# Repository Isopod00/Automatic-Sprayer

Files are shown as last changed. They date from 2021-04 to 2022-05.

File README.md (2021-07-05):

# Automatic Sprayer
Created By Anthony Brogni

This is my Automatic Sprayer project. I originally made a prototype of this project in 2017 but was not completely satisfied with the results, so I decided to go back and improve it. I have been making changes to this project ever since, and I believe it has been greatly improved over the past four years. This project is an Arduino-controlled automatic sprayer that can keep plants and pets hydrated while you're away from home. When you first plug it in you are prompted to configure the system, and then after that, you're good to go! Some features of this project are spray scheduling and spray duration control, a visual countdown clock to the next spray, and a manual spray button. Another notable feature that I recently added is Wifi connectivity so that the project can connect to the user's home Wifi network, enabling over-the-air software updates. In addition to over-the-air software updates, Wifi connectivity also allows the project to connect to the Adafruit IO web service for control over wifi. This means that by using my phone from anywhere in the world, as long as I am connected to the internet, I can trigger the sprayer to start spraying! Using the IFTTT service, I have also connected the project to Amazon Alexa, allowing me to trigger sprays by giving a voice command to my Alexa-enabled devices. As you can see, there are multiple ways to control my automatic sprayer project, which makes it easy and convenient to use for everyone!

<p align="center">
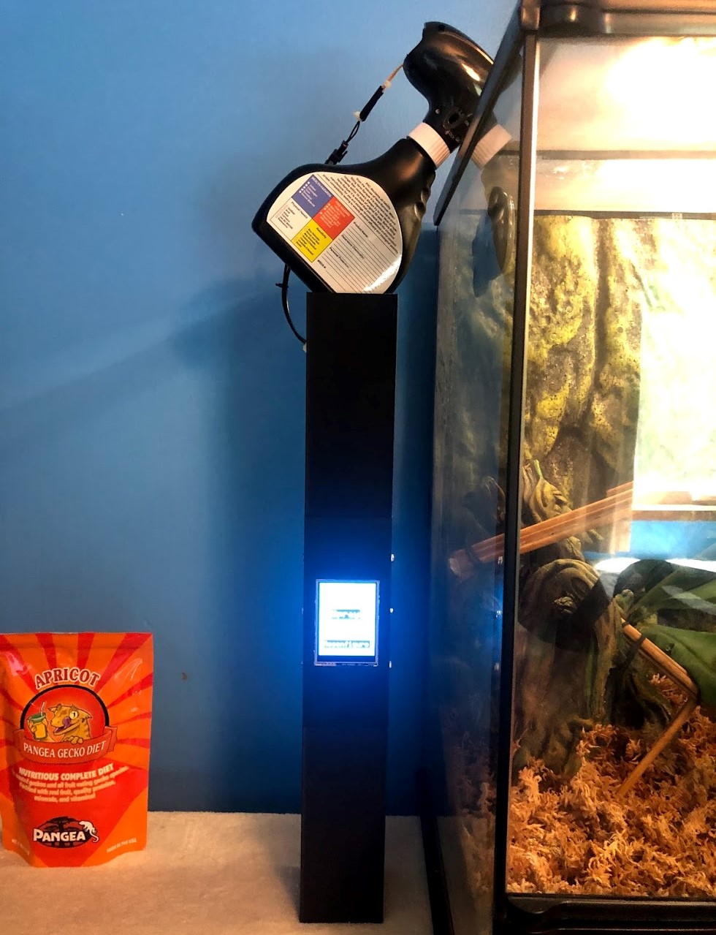
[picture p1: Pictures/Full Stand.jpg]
Sprayer Stand
   
</p>

### Code

All of the code for this project is contained in a single [.ino script](https://github.com/Isopod00/Automatic-Sprayer/blob/Wifi-Enabled/Code/AutomaticSprayer/AutomaticSprayer.ino) that is run by an Arduino Mega 2560. 

The main functions of the code are to:
  1. Connect to my home wifi network to allow for over-the-air software updates
  2. Connect to the Adafruit IO service to allow for commands to be sent over Wifi
  3. Allow the user to configure system settings such as the interval between sprays and the spray duration using the touch screen
  4. Keep track of the time remaining until the next spray and display it to the user on the touch screen
  5. Allow the user to manually initiate a spray whenever they want via a digital button on the touch screen

The code for this project utilizes the Elegoo_GFX, Elegoo_TFTLCD, Touchscreen, WiFi101, ArduinoOTA, and Adafruit_MQTT libraries, all of which can be found [here](https://github.com/Isopod00/Automatic-Sprayer/tree/Wifi-Enabled/Code/Libraries) in the project repository. The SPI library is also used, which is included in the Arduino IDE by default.

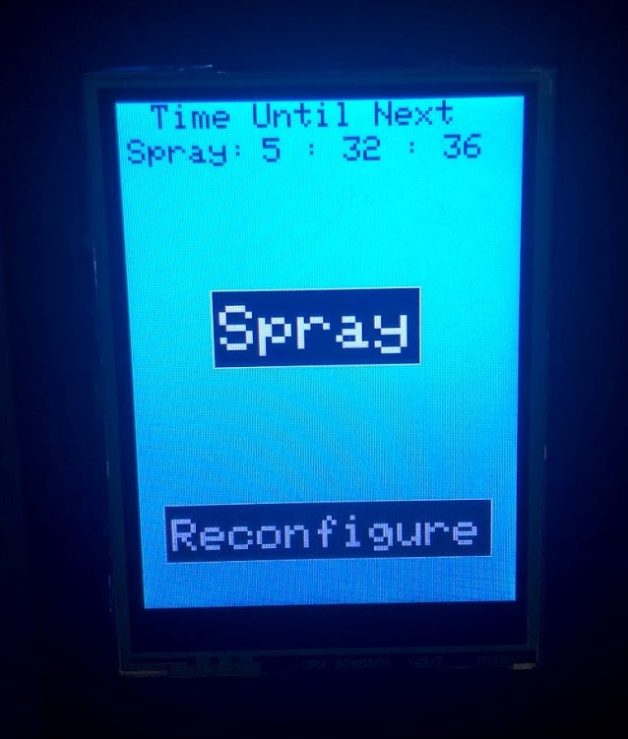
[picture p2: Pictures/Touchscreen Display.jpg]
Touchscreen Display
 

<p>&nbsp;</p>

### Electronics

The electronic components used in this project are:
  1. [Arduino MEGA 2560 REV3](https://www.amazon.com/ELEGOO-ATmega2560-ATMEGA16U2-Projects-Compliant/dp/B01H4ZLZLQ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)
  2. [ELEGOO 2.8 Inch TFT LCD Touch Screen](https://www.amazon.com/Elegoo-EL-SM-004-Inches-Technical-Arduino/dp/B01EUVJYME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)
  3. [L298N Motor Driver Board](https://www.amazon.com/HiLetgo-Controller-Stepper-H-Bridge-Mega2560/dp/B07BK1QL5T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)
  4. [3.3v/5v Power Supply Module](https://www.amazon.com/JBtek-Breadboard-Supply-Arduino-Solderless/dp/B010UJFVTU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)
  5. [Motorized Spray Bottle](https://www.amazon.com/Dynamic-1-touch-multi-purpose-motorized-bottle/dp/B01LXJ0SPG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)
  6. [ELEGOO 9V 1A Barrel Plug Power Adapter](https://www.amazon.com/ELEGOO-100V-240V-Converter-Adapter-Certificate/dp/B074BRR5YN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)
  7. [DC Barrel Plug Splitter](https://www.amazon.com/PHC-DC-3Y-Barrel-Splitter-Female/dp/B009AZZ4ES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)
  8. [Flexible Breadboard Jumper Wires](https://www.amazon.com/Elegoo-EL-CP-004-Multicolored-Breadboard-arduino/dp/B01EV47GI4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)
  9. [Adafruit ATWINC1500 WiFi Breakout Board](https://www.amazon.com/Adafruit-2999-ATWINC1500-WiFi-Breakout/dp/B01GVI1NKA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)

<p>&nbsp;</p><p>&nbsp;</p><p>&nbsp;</p>

<p align="center">
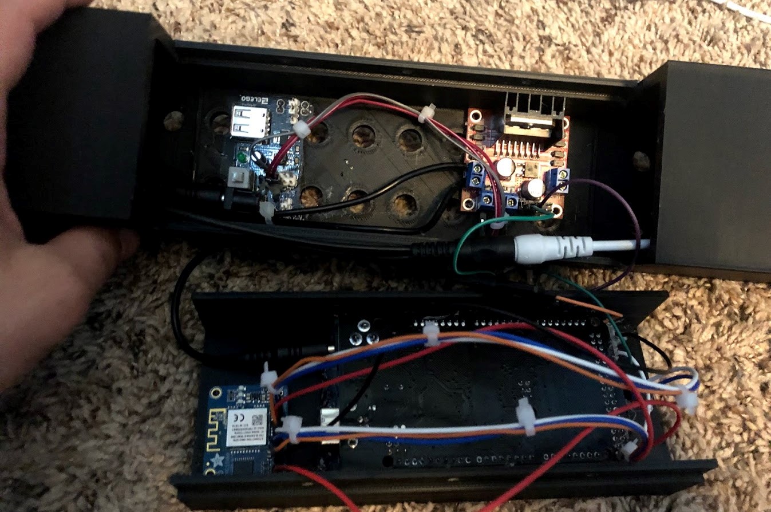
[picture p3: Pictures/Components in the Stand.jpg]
Electronic Components
   
</p>

### 3D Printed Parts

For this project I designed and 3D Printed a stand for the sprayer that also houses the electronics inside of it to keep everything compact.
 
<p align="center">
  <b>CAD Program Used:</b> Fusion 360 &nbsp;&nbsp;&nbsp;&nbsp;&nbsp;
  <b>Slicer Program Used:</b> Ultimaker Cura <br>                                             
  <b>3D Printer Used:</b> Ender 5 Pro &nbsp;&nbsp;&nbsp;&nbsp;&nbsp;
  <b>Filament Used:</b> Black PLA <br><br>
  All of the STL and sliced G-Code files can be found <a href="https://github.com/Isopod00/Automatic-Sprayer/tree/Wifi-Enabled/CAD%20Files">here</a> in the project repository.
</p>

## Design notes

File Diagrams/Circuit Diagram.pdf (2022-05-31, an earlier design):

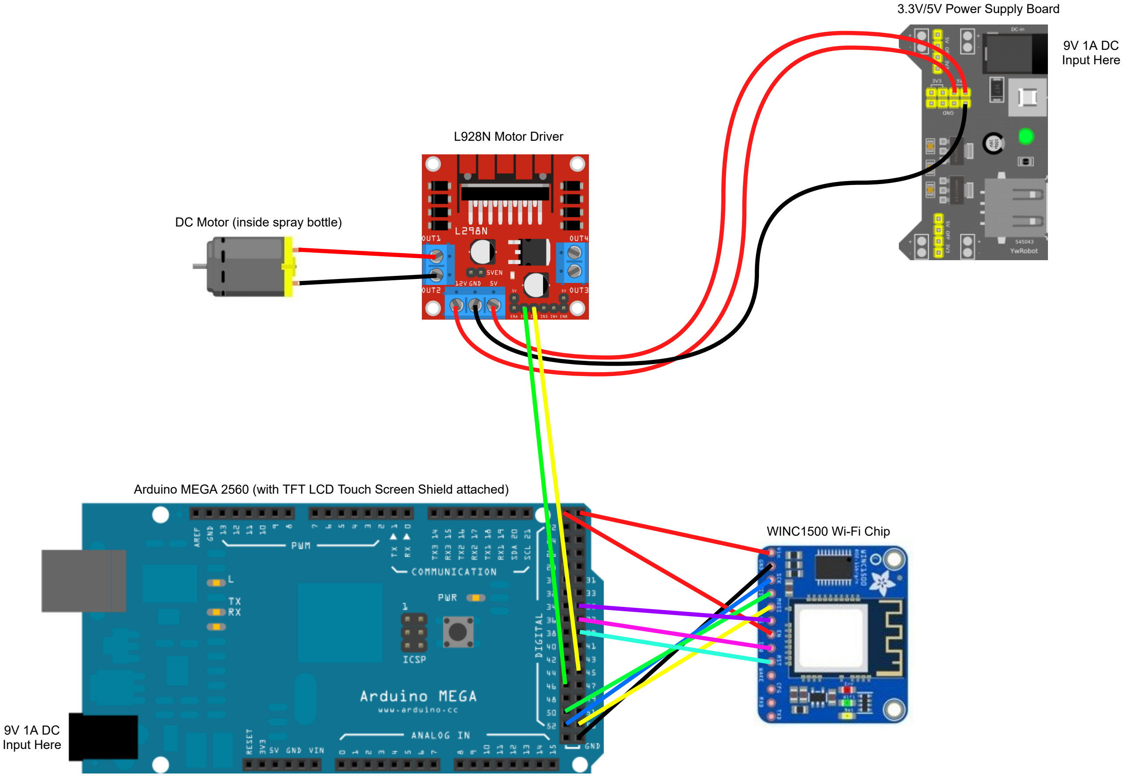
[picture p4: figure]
L928N Motor Driver; DC Motor (inside spray bottle); WINC1500 Wi-Fi Chip; 3.3V/5V Power Supply Board; 9V 1A DC Input Here

Arduino MEGA 2560 (with TFT LCD Touch Screen Shield attached)

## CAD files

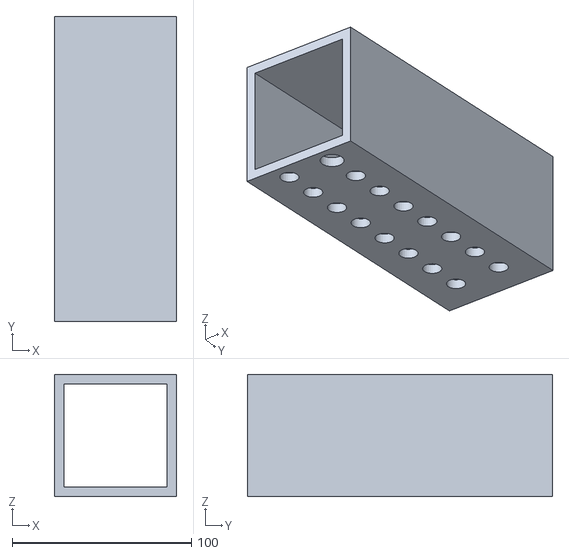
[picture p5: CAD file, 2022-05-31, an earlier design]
CAD Files/STL Files/Stand_Base.stl
68.0 x 170.0 x 68.0

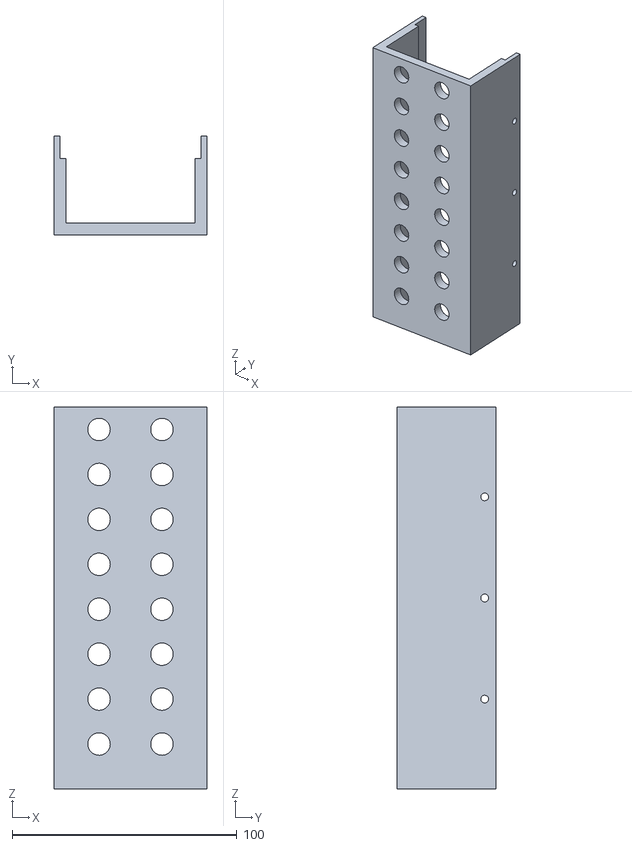
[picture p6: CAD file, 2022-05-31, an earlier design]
CAD Files/STL Files/Stand_Electronics_Back.stl
68.0 x 44.0 x 170.0

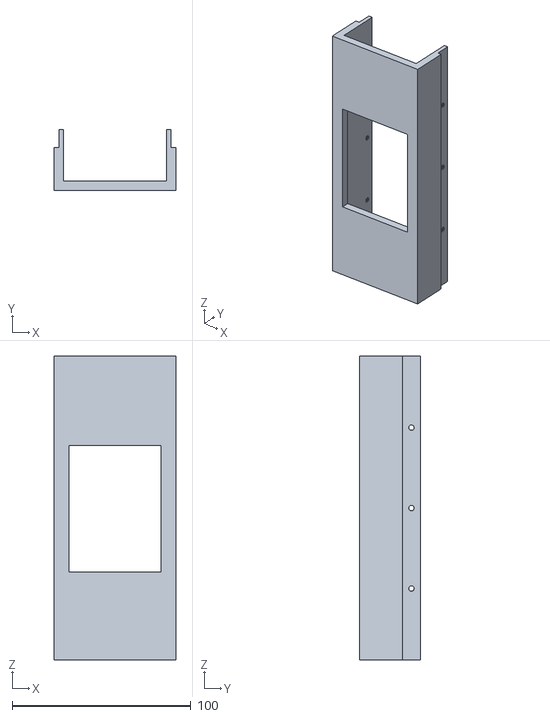
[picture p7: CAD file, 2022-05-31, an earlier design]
CAD Files/STL Files/Stand_Electronics_Front.stl
68.0 x 34.0 x 170.0

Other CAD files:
CAD Files/STL Files/Stand_Top.stl

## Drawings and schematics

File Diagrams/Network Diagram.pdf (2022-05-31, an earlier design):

# Cloud Services

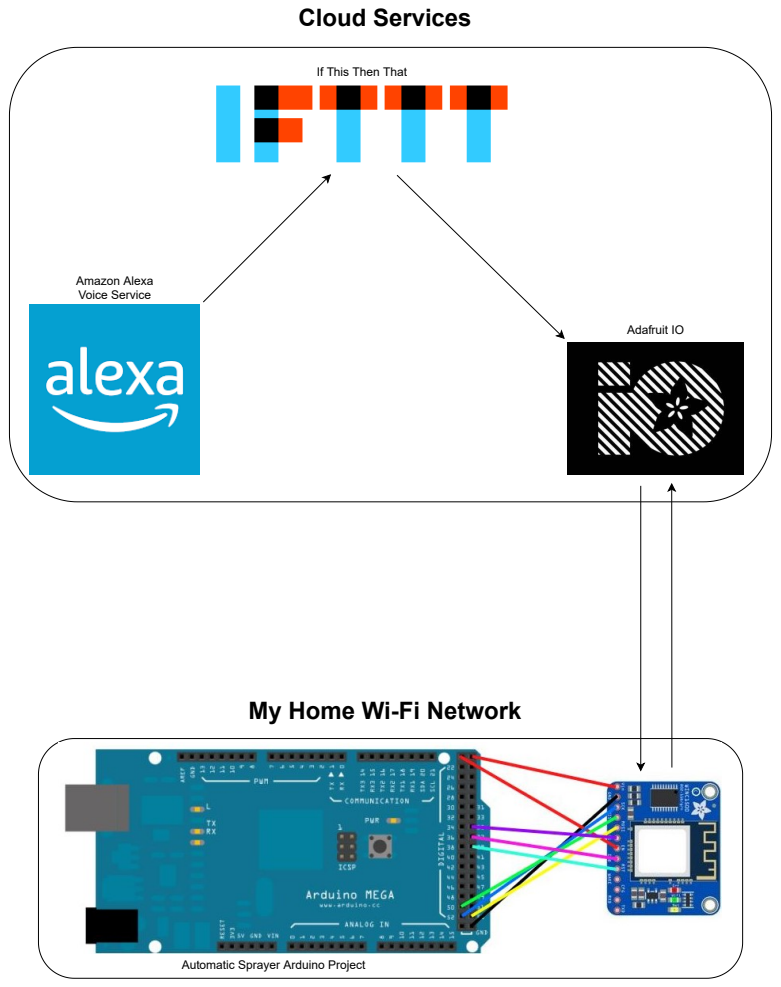
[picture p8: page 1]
Amazon Alexa Voice Service; Adafruit IO

If This Then That

My Home Wi-Fi Network

Automatic Sprayer Arduino Project

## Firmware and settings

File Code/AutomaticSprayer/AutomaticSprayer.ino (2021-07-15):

//Automatic Sprayer
//By Anthony Brogni

#include <Elegoo_GFX.h>    // Core graphics library
#include <Elegoo_TFTLCD.h> // Hardware-specific library
#include <TouchScreen.h>   // Core (non-specific) touchscreen library

// Libraries required for WiFi connectivity & OTA updates //
#include <SPI.h>
#include <WiFi101.h>
#include <ArduinoOTA.h>

// Libraries Required for integration with Adafruit.io //
#include "Adafruit_MQTT.h"
#include "Adafruit_MQTT_Client.h"

// Enter sensitive data (like WiFi name & password) in the secrets tab (arduino_secrets.h) //
#include "arduino_secrets.h" 

// Wifi Settings //
char ssid[] = SECRET_SSID; // WiFi network SSID (name)
char pass[] = SECRET_PASS; // WiFi network password
int status = WL_IDLE_STATUS;

// Adafruit.io Settings //
#define AIO_SERVER      "io.adafruit.com"
#define AIO_SERVERPORT  1883
#define AIO_USERNAME    SECRET_USERNAME
#define AIO_KEY         SECRET_KEY

//Set up the wifi client
WiFiClient client;
Adafruit_MQTT_Client mqtt(&client, AIO_SERVER, AIO_SERVERPORT, AIO_USERNAME, AIO_KEY);

#define MQTT_CONN_KEEPALIVE 43200; //The server will keep the socket open, unless it has not heard from the device in 12 hours

// Adafruit.io Feeds //
Adafruit_MQTT_Subscribe sprayStatus = Adafruit_MQTT_Subscribe(&mqtt, AIO_USERNAME "/feeds/spraying");
Adafruit_MQTT_Publish confirmSpray = Adafruit_MQTT_Publish(&mqtt, AIO_USERNAME "/feeds/sprayconfirmed");

const int totalSprayTime = 825; // Measured in seconds
int remainingSprays;

// The control pins for the LCD can be assigned to any digital or analog pins, but using the analog pins allows for doubling up the pins with the touch screen (see the TFT paint example).
#define LCD_CS A3 // Chip Select goes to Analog 3
#define LCD_CD A2 // Command/Data goes to Analog 2
#define LCD_WR A1 // LCD Write goes to Analog 1
#define LCD_RD A0 // LCD Read goes to Analog 0

#define LCD_RESET A4 // Can alternately just connect to Arduino's reset pin

#define YP A2  // must be an analog pin, use "An" notation!
#define XM A3  // must be an analog pin, use "An" notation!
#define YM 8   // can be a digital pin
#define XP 9   // can be a digital pin

// The min and max values for the x and y coordinates of the touchscreen //
#define TS_MINX 130
#define TS_MINY 130
#define TS_MAXX 940
#define TS_MAXY 940

// Assign human-readable names to some common 16-bit color values //
#define BLACK   0x0000
#define BLUE    0x001F
#define RED     0xF800
#define GREEN   0x07E0
#define CYAN    0x07FF
#define MAGENTA 0xF81F
#define YELLOW  0xFFE0
#define WHITE   0xFFFF

#define BACKGROUNDCOLOR CYAN // Customize the background color of the display!
#define TEXTCOLOR BLACK // Customize the color of text that is displayed!

Elegoo_TFTLCD tft(LCD_CS, LCD_CD, LCD_WR, LCD_RD, LCD_RESET);
TouchScreen ts = TouchScreen(XP, YP, XM, YM, 300);

int hours = 8;
int minutes = 0;
int seconds = 0;

int time = 0;
int waitTime = 0;
int wait = 15000;

int motor = 46;
int motorPin2 = 45;

bool spraying = false;

int assignedHours = 8;
int assignedWait = 15000;

bool answered1 = false;
bool answered2 = false;
bool answered3 = false;
bool answered4 = false;

void setup() {
  WiFi.setPins(35,37,39); // Configure pins for the Adafruit ATWINC1500 Breakout
  
  Serial.begin(9600); // Initialize serial 

  connectToNetwork(); // Connect to home WiFi network

  tft.reset();

  pinMode(motor, OUTPUT);
  pinMode(motorPin2, OUTPUT);

  digitalWrite(motorPin2, LOW);

  mqtt.subscribe(&sprayStatus);

  uint16_t identifier = tft.readID();
  if (identifier == 0x9325) {
  } else if (identifier == 0x9328) {
  } else if (identifier == 0x4535) {
  } else if (identifier == 0x7575) {
  } else if (identifier == 0x9341) {
  } else if (identifier == 0x8357) {
  } else if (identifier == 0x0101) {
    identifier = 0x9341;
  }
  else {
    identifier = 0x9341;
  }
  tft.begin(identifier);
  
  boot();
  configSystem();

  remainingSprays = totalSprayTime / (assignedWait / 1000); // divide by 1000 converts milliseconds to seconds
}

void loop() {
  if (status == WL_CONNECTED) { 
    ArduinoOTA.poll(); // Check for OTA updates over WiFi
    MQTT_connect(); // Connect or Reconnect to the MQTT service
  } else {
    connectToNetwork(); // Try reconnecting to home WiFi network
  }
  
  Adafruit_MQTT_Subscribe *subscription;
  subscription = mqtt.readSubscription();

  if (subscription == &sprayStatus) {
    if (0 == strcmp((char *)sprayStatus.lastread, "ON")) {
      spray();
    }
  }

  // Check for button presses and add time to the loop so counting by seconds is accurate //
  buttonPress();
  delay(5);
  if (time == 60) {
    time = 0;
    subtractTime();
  }
  else {
    time++;
  }
}

void connectToNetwork() {
  // Check if the WiFi board is connected //
  if (WiFi.status() != WL_NO_SHIELD) {
    
    // Attempt to connect to Wifi network //
  while (status != WL_CONNECTED) {
    Serial.print("Attempting to connect to SSID: ");
    Serial.println(ssid);
    status = WiFi.begin(ssid, pass); // Connect to WPA/WPA2 network. Change this line if using open or WEP network
  }
  
  Serial.print("Successfully connected to SSID: ");
  Serial.print(WiFi.SSID());
  Serial.println("!");

  // start the WiFi OTA library with internal (flash) based storage
  ArduinoOTA.begin(WiFi.localIP(), "Arduino", "password", InternalStorage);
  }
}
  
void boot() {
  tft.fillScreen(BACKGROUNDCOLOR);
  tft.setRotation(2);
  tft.setCursor(20, 2);
  tft.setTextColor(TEXTCOLOR);
  tft.setTextSize(2);
  tft.println("Automatic Sprayer");
  tft.setCursor(100, 22);
  tft.println("v3.5");
  tft.setCursor(80, 280);
  tft.println("Made by");
  tft.setCursor(40, 300);
  tft.println("Anthony Brogni");
  tft.setCursor(30, 140);
  tft.setTextSize(4);
  tft.println("Welcome!");
  delay(4000);
}

// Function used to connect and reconnect as necessary to the MQTT server //
void MQTT_connect() {
  // Stop if already connected.
  if (mqtt.connected()) {
    return;
  }

  Serial.print("Connecting to MQTT... ");

  if(mqtt.connect() == 0) {
    Serial.println("MQTT Connected!");
  } else {
    Serial.println("Connect to MQTT FAILED");
  }
}

void configSystem() {
  assignedHours = 8;
  assignedWait = 15000;

  tft.fillScreen(BACKGROUNDCOLOR);
  tft.setCursor(20, 2);
  tft.setTextSize(2);
  tft.println("The default spray");
  tft.setCursor(15, 22);
  tft.println("interval is every");
  tft.setCursor(50, 42);
  tft.println("eight hours.");
  tft.setCursor(20, 102);
  tft.println("Would you like it");
  tft.setCursor(20, 122);
  tft.println("to stay that way?");
  drawButton(20, 210, 80, 50, 4, "Yes", 0);
  drawButton(140, 210, 80, 50, 4, "No", 15);
  while (!answered1) {
    if (status == WL_CONNECTED) { 
      ArduinoOTA.poll(); //Check for WiFi OTA updates
    }
  
    TSPoint p = ts.getPoint();

    if (p.z > ts.pressureThreshhold) {
      if (p.x > 280 && p.x < 400 && p.y > 185 && p.y < 420) {
        //This is important because the tft and touchscreen libraries are sharing pins
        pinMode(XM, OUTPUT);
        pinMode(YP, OUTPUT);

        answered1 = true;

        tft.fillScreen(BACKGROUNDCOLOR);
        config2();
      }
      else if (p.x > 255 && p.x < 385 && p.y > 610 && p.y < 860) {
        //This is important because the tft and touchscreen libraries are sharing pins
        pinMode(XM, OUTPUT);
        pinMode(YP, OUTPUT);

        answered1 = true;

        tft.fillScreen(BACKGROUNDCOLOR);

        tft.setCursor(0, 0);
        tft.setTextSize(2);
        tft.println("How many hours would");
        tft.setCursor(5, 20);
        tft.println("you like to set the");
        tft.setCursor(10, 40);
        tft.println("spray interval to?");

        drawButton(15, 120, 50, 50, 4, "2", 8);
        drawButton(95, 120, 50, 50, 4, "4", 8);
        drawButton(175, 120, 50, 50, 4, "6", 8);
        drawButton(15, 200, 50, 50, 4, "8", 8);
        drawButton(95, 200, 50, 50, 4, "10", -3);
        drawButton(175, 200, 50, 50, 4, "12", -3);

        while (!answered2) {
          if (status == WL_CONNECTED) { 
            ArduinoOTA.poll(); //Check for WiFi OTA updates
          }
  
          TSPoint p = ts.getPoint();

          if (p.z > ts.pressureThreshhold) {
            //This is important because the tft and touchscreen libraries are sharing pins
            pinMode(XM, OUTPUT);
            pinMode(YP, OUTPUT);
            
            if (p.x > 520 && p.x < 640 && p.y > 180 && p.y < 295) {
              answered2 = true;
              assignedHours = 2;
            }
            else if (p.x > 520 && p.x < 640 && p.y > 445 && p.y < 580) {
              answered2 = true;
              assignedHours = 4;
            }
            else if (p.x > 520 && p.x < 640 && p.y > 700 && p.y < 850) {
              answered2 = true;
              assignedHours = 6;
            }
            else if (p.x > 285 && p.x < 430 && p.y > 180 && p.y < 295) {
              answered2 = true;
              assignedHours = 8;
            }
            else if (p.x > 285 && p.x < 430 && p.y > 445 && p.y < 580) {
              answered2 = true;
              assignedHours = 10;
            }
            else if (p.x > 285 && p.x < 430 && p.y > 700 && p.y < 850) {
              answered2 = true;
              assignedHours = 12;
            }
            if (answered2) {
              tft.fillScreen(BACKGROUNDCOLOR);
              config2();
            }
          }
        }
      }
    }
  }
}

void subtractTime() {
  if (seconds == 0) {
    if (minutes == 0) {
      if (hours == 0) {
        if (!spraying) {
          tft.fillRect(72, 19, 250, 18, BACKGROUNDCOLOR);
        }
        digitalWrite(motor, HIGH);
        delay(wait);
        digitalWrite(motor, LOW);

        hours = assignedHours;
        minutes = 0;
        seconds = 0;
      }
      else {
        if (!spraying) {
          tft.fillRect(72, 19, 250, 18, BACKGROUNDCOLOR);
        }
        hours = hours - 1;
        minutes = 59;
        seconds = 59;
      }
    }
    else {
      if (!spraying) {
        tft.fillRect(72, 19, 250, 18, BACKGROUNDCOLOR);
      }
      minutes = minutes - 1;
      seconds = 59;
    }
  }
  else {
    if (!spraying) {
      tft.fillRect(72, 19, 250, 18, BACKGROUNDCOLOR);
    }
    seconds = seconds - 1;
  }
  if (hours == 0) {
    if (minutes == 0) {
      if (seconds == 0) {
        if (!spraying) {
          tft.fillRect(0, 0, 300, 50, BACKGROUNDCOLOR);
        }
        tft.setTextSize(2);
        tft.setCursor(10, 20);
        tft.print("Spraying Enclosure");
        confirmSpray.publish(1.0);

        digitalWrite(motor, HIGH);
        delay(wait);
        digitalWrite(motor, LOW);

        confirmSpray.publish(0.0);
        remainingSprays--;
        
        hours = assignedHours;
        minutes = 0;
        seconds = 0;
      }
    }
    if (!spraying) {
      tft.fillRect(0, 19, 300, 18, BACKGROUNDCOLOR);
    }
  }
  if (!spraying) {
    tft.setTextSize(2);
    tft.setCursor(20, 1);
    tft.print("Time Until Next");
    tft.setCursor(5, 21);
    tft.print("Spray: ");
    tft.setCursor(85, 21); 
    tft.print(hours);
    tft.print(" : ");
    tft.print(minutes);
    tft.print(" : ");
    tft.print(seconds);
  }
}

void spray(){
   spraying = true;
   confirmSpray.publish(1.0);
   
   tft.fillRect(0, 0, 300, 50, BACKGROUNDCOLOR);
   tft.setTextSize(2);
   tft.setCursor(10, 20);
   tft.print("Spraying Enclosure");
   digitalWrite(motor, HIGH);
   while (spraying) {
      delay(1000);
      subtractTime();
      waitTime = waitTime + 1000;
      if (waitTime == wait) {
        waitTime = 0;
        digitalWrite(motor, LOW);
        spraying = false;
        confirmSpray.publish(0.0);
        remainingSprays--;
      }
    }
    tft.fillRect(0, 15, 300, 30, BACKGROUNDCOLOR);
    tft.setCursor(20, 1);
    tft.print("Time Until Next");
    tft.setCursor(5, 21);
    tft.print("Spray: ");
}

void endConfig() {
  wait = assignedWait;
  hours = assignedHours;
  tft.fillScreen(BACKGROUNDCOLOR);
  tft.setTextSize(2);
  tft.setCursor(20, 1);
  tft.print("Time Until Next");
  tft.setCursor(5, 21);
  tft.print("Spray: ");
  tft.print(hours);
  tft.print(" : ");
  tft.print(minutes);
  tft.print(" : ");
  tft.print(seconds);
  drawButton(50, 112, 130, 50, 4, "Spray", 0);
  drawButton(15, 250, 210, 40, 3, "Reconfigure", 0);
}

void drawButton(int x1, int y1, int width, int height, int textSize, String text, int textOffset) {
  tft.setTextColor(WHITE);
  tft.fillRect(x1, y1, width, height, BLACK);
  tft.drawRect(x1, y1, width, height, WHITE);
  tft.setCursor(x1 + 5 + textOffset, y1 + 10);
  tft.setTextSize(textSize);
  tft.print(text);
  tft.setTextColor(TEXTCOLOR);
}

void buttonPress() {
  TSPoint p = ts.getPoint();

  if (p.z > ts.pressureThreshhold) {
    //This is important because the tft and touchscreen libraries are sharing pins
    pinMode(XM, OUTPUT);
    pinMode(YP, OUTPUT);
    
    if (p.x > 190 && p.x < 260 && p.y > 180 && p.y < 860) {
      hours = 8;
      minutes = 0;
      seconds = 0;

      answered1 = false;
      answered2 = false;
      answered3 = false;
      answered4 = false;

      configSystem();
    }
    if (p.x > 520 && p.x < 660 && p.y > 295 && p.y < 705) {
      spray();
    }
  }
  //This is important because the tft and touchscreen libraries are sharing pins
  pinMode(XM, OUTPUT);
  pinMode(YP, OUTPUT);
}

void config2()
{
  tft.setCursor(20, 2);
  tft.setTextSize(2);
  tft.println("The default spray");
  tft.setCursor(5, 22);
  tft.println("duration is fifteen");
  tft.setCursor(80, 42);
  tft.println("seconds.");
  tft.setCursor(15, 102);
  tft.println("Would you like it ");
  tft.setCursor(15, 122);
  tft.println("to stay that way?");
  drawButton(20, 210, 80, 50, 4, "Yes", 0);
  drawButton(140, 210, 80, 50, 4, "No", 15);

  while (!answered3) {
    if (status == WL_CONNECTED) { 
      ArduinoOTA.poll(); //Check for WiFi OTA updates
    }
  
    TSPoint p = ts.getPoint();

    if (p.z > ts.pressureThreshhold) {
      if (p.x > 280 && p.x < 400 && p.y > 185 && p.y < 420) {
        //This is important because the tft and touchscreen libraries are sharing pins
        pinMode(XM, OUTPUT);
        pinMode(YP, OUTPUT);

        answered3 = true;
        endConfig();
      }
      else if (p.x > 255 && p.x < 385 && p.y > 610 && p.y < 860) {
        //This is important because the tft and touchscreen libraries are sharing pins
        pinMode(XM, OUTPUT);
        pinMode(YP, OUTPUT);

        tft.fillScreen(BACKGROUNDCOLOR);

        answered3 = true;

        tft.setCursor(20, 0);
        tft.setTextSize(2);
        tft.println("How many seconds");
        tft.setCursor(15, 20);
        tft.println("would you like to");
        tft.setCursor(40, 40);
        tft.println("set the spray");
        tft.setCursor(45, 60);
        tft.println("duration to?");

        drawButton(15, 120, 55, 50, 4, "5", 10);
        drawButton(95, 120, 55, 50, 4, "10", 0);
        drawButton(175, 120, 55, 50, 4, "15", 0);
        drawButton(14, 200, 55, 50, 4, "20", 0);
        drawButton(94, 200, 55, 50, 4, "25", 0);
        drawButton(174, 200, 55, 50, 4, "30", 0);

        while (!answered4) {
          if (status == WL_CONNECTED) { 
            ArduinoOTA.poll(); //Check for WiFi OTA updates
          }
  
          TSPoint p = ts.getPoint();

          if (p.z > ts.pressureThreshhold) {
            if (p.x > 520 && p.x < 640 && p.y > 180 && p.y < 295) {
              //This is important because the tft and touchscreen libraries are sharing pins
              pinMode(XM, OUTPUT);
              pinMode(YP, OUTPUT);

              answered4 = true;
              assignedWait = 5000;
            }
            else if (p.x > 520 && p.x < 640 && p.y > 445 && p.y < 580) {
              //This is important because the tft and touchscreen libraries are sharing pins
              pinMode(XM, OUTPUT);
              pinMode(YP, OUTPUT);

              answered4 = true;
              assignedWait = 10000;
            }
            else if (p.x > 520 && p.x < 640 && p.y > 700 && p.y < 850) {
              //This is important because the tft and touchscreen libraries are sharing pins
              pinMode(XM, OUTPUT);
              pinMode(YP, OUTPUT);

              answered4 = true;
              assignedWait = 15000;
            }
            else if (p.x > 285 && p.x < 430 && p.y > 180 && p.y < 295) {
              //This is important because the tft and touchscreen libraries are sharing pins
              pinMode(XM, OUTPUT);
              pinMode(YP, OUTPUT);

              answered4 = true;
              assignedWait = 20000;
            }
            else if (p.x > 285 && p.x < 430 && p.y > 445 && p.y < 580) {
              //This is important because the tft and touchscreen libraries are sharing pins
              pinMode(XM, OUTPUT);
              pinMode(YP, OUTPUT);

              answered4 = true;
              assignedWait = 25000;
            }
            else if (p.x > 285 && p.x < 430 && p.y > 700 && p.y < 850) {
              //This is important because the tft and touchscreen libraries are sharing pins
              pinMode(XM, OUTPUT);
              pinMode(YP, OUTPUT);

              answered4 = true;
              assignedWait = 30000;
            }
            if (answered4) {
             endConfig();
            }
          }
        }
      }
    }
  }
}

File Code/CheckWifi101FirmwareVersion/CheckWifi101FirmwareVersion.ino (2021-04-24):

/*
 * This example check if the firmware loaded on the WiFi101
 * shield is updated.
 *
 * Circuit:
 * - WiFi101 Shield attached
 *
 * Created 29 July 2015 by Cristian Maglie
 * This code is in the public domain.
 */
#include <SPI.h>
#include <WiFi101.h>
#include <driver/source/nmasic.h>

void setup() {
  //Configure pins for Adafruit ATWINC1500 Breakout
  WiFi.setPins(35,37,39);

  // Initialize serial
  Serial.begin(9600);
  while (!Serial) {
    ; // wait for serial port to connect. Needed for native USB port only
  }

  // Print a welcome message
  Serial.println("WiFi101 firmware check.");
  Serial.println();

  // Check for the presence of the shield
  Serial.print("WiFi101 shield: ");
  if (WiFi.status() == WL_NO_SHIELD) {
    Serial.println("NOT PRESENT");
    return; // don't continue
  }
  Serial.println("DETECTED");

  // Print firmware version on the shield
  String fv = WiFi.firmwareVersion();
  String latestFv;
  Serial.print("Firmware version installed: ");
  Serial.println(fv);

  if (REV(GET_CHIPID()) >= REV_3A0) {
    // model B
    latestFv = WIFI_FIRMWARE_LATEST_MODEL_B;
  } else {
    // model A
    latestFv = WIFI_FIRMWARE_LATEST_MODEL_A;
  }

  // Print required firmware version
  Serial.print("Latest firmware version available : ");
  Serial.println(latestFv);

  // Check if the latest version is installed
  Serial.println();
  if (fv >= latestFv) {
    Serial.println("Check result: PASSED");
  } else {
    Serial.println("Check result: NOT PASSED");
    Serial.println(" - The firmware version on the shield do not match the");
    Serial.println("   version required by the library, you may experience");
    Serial.println("   issues or failures.");
  }
}

void loop() {
  // do nothing
}

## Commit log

2021-04-16 Clean Up
    -Renamed "times" and "waitTimes" variables to "time" and "waitTime" because it makes way more sense
    -Switched to the simpler declaration of a Elegoo_TFTLCD object (Since I am using the shield, all data and control lines are fixed and don't need to be defined)
    -Added a few helpful comments
    -Deleted many pin number declarations since I am using the simpler declaration for the tft lcd now
    [AutomaticSprayer.ino]
2021-04-17 Organized CAD Files Better
    [Stand_Base.stl, Stand_Electronics_Back.stl, Stand_Electronics_Front.stl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]
2021-04-19 Switch from "Shield" to "Breakout Board"
    I was unable to purchase a WINC1500 shield and instead purchased a breakout board with the WINC1500, so the code will be (slightly) different
    -Renamed all instances of "Shield" to "Board"
    -Added the WiFi libraries to the Libraries folder of the project
    -Added a call to the setPins() method to configure the pins used by the WiFi breakout board
2021-04-19 Organize CAD Files
    I already did this in the new version 3.0 branch but wanted to do it in the master branch too
    [Stand_Base.stl, Stand_Electronics_Back.stl, Stand_Electronics_Front.stl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]
2021-04-21 Update WiFi Breakout Pin Numbers
2021-04-24 Manually reset wifi board
    [AutomaticSprayer.ino]
2021-04-24 Added ArduinoOTA library to project folder
2021-04-24 Fixed code by adding LCD pin declarations back
    [AutomaticSprayer.ino]
2021-04-24 Fixed relay pin number
    [AutomaticSprayer.ino]
2021-04-25 Allow for the customization of text color
    I also greatly simplified the process of drawing buttons on the screen!
2021-04-30 Code Updates
    -Changed the version # to 3.0
    -Made all buttons look nicer by adding a textOffset parameter to the drawButton() method
    -Removed the "please take a moment to configure your system!" and "configuration is complete!" screens because they were cheesy and irrelevant, looked bad visually, and just wasted time and made the system feel less responsive. It feels so much snappier now!
    [AutomaticSprayer.ino]
2021-05-02 Reorganized some code and added missing comments
    [AutomaticSprayer.ino]
2021-05-02 Improved the look of the reconfigure button
2021-05-02 Made reconfigure button easier to press
2021-06-10 Reorganized folder structure & changed from using a relay to a motor driver
2021-06-14 Reversed direction of the motor, this fixed a leaking issue!
    [AutomaticSprayer.ino]
2021-06-28 fixed Green background color
    [AutomaticSprayer.ino]
2021-07-05 It works!!
    Some things need to be fixed though
    [AutomaticSprayer.ino]
2021-07-06 Increase MQTT keepalive time
    Essentially, force the server to keep the socket open
